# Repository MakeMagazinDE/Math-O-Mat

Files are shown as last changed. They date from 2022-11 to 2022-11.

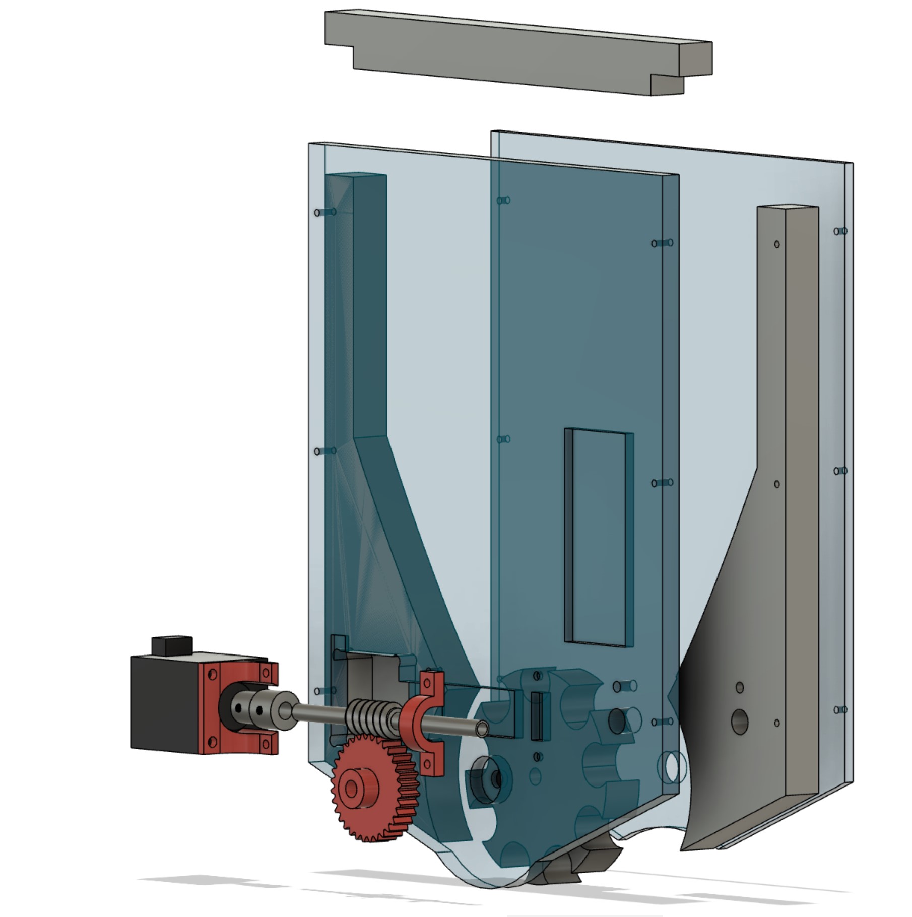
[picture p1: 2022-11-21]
Hardware/Explosionszeichnung.jpg

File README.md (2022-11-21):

GitHub Logo

Maker Media GmbH
*** 

# Math-O-Mat

stellt Übungsaufgaben fürs Kopfrechnen per Web-Quiz und belohnt richtige Antworten mit M&Ms.



Den vollständigen Artikel mit der Bauanleitung gibt es in der **[Make-Ausgabe 6/22 ab Seite 10](https://www.heise.de/select/make/2022/6/2216407360229342785) ** zu lesen

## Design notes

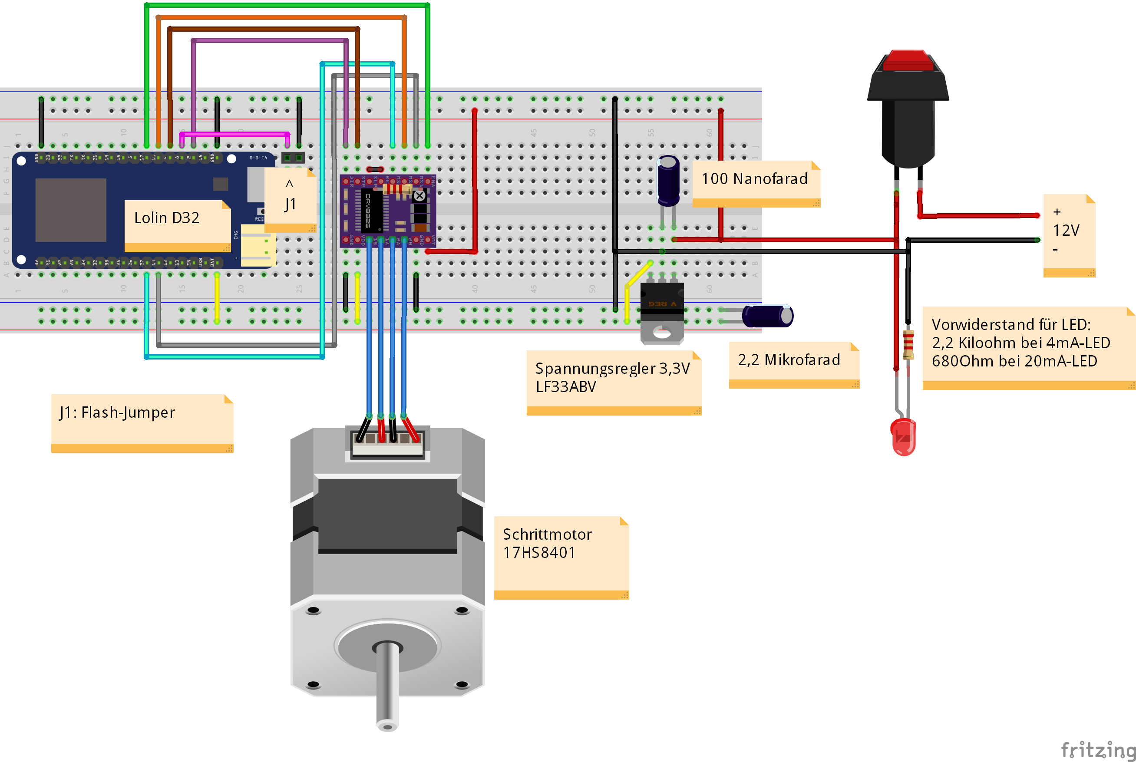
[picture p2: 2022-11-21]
Elektronik/MathOMat_Breadboard_Steckplatine.png

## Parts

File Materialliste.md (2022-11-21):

# Material

**Mechanik**

* Rückwand: Siebdruckplatte 270mm :x 360mm :x 10mm, Alternative für Laubsäge und Lasercutter: 2 Stück gleicher Maße aus  5mm MDF oder Sperrholz
* Trichter und Portionierer: Buche 230mm :x 415mm :x 20mm, Alternative für Laubsäge und Lasercutter: 4 Stück gleicher Maße aus  5mm MDF oder Sperrholz
* Acrylglas 255mm :x 325mm :x 5mm
* Gestell: Siebdruckplatte 290mm :x 250mm :x 10mm, Alternative für Laubsäge und Lasercutter: 2 Stück gleicher Maße aus  5mm MDF oder Sperrholz
* Aluminiumrohr 8mm als Achse für Schneckengetriebe
* Sechskantschraube M8x50, Gewindelänge 40mm, alternativ Gewindestange 50mm mit zwei gekonterten Muttern als Kopf, als Achse für den Portionierer 
* Stellschraube M4, ggf. auch eine Madenschraube
* 2 Kugellager Innendurchmesser 8mm, Aussendurchmesser 22 mm, Dicke 7mm
* 6 Schrauben M3x40mm mit Unterlegscheiben und Muttern
* Befestigungsmaterial für die Platine, etwa Schrauben, Distanzhülsen etc.
* 3D-Druckteile: Schnecke, Lagerhalter, Portioniererzahnrad, Motorhalter, Motorkupplung
* Holzschrauben mit Unterlegscheiben max 10mm lang (für die Deckplatte)
* Plastikstreifen 20mm breit, etwa 50 bis 80mm lang, als elastische Spaltabdeckung, etwa aus der Hülle eines Schnellhefters oder einer Plastikverpackung geschnitten –das Plastik muss einfach stabil genug sein, um überschüssige M&Ms abzustreifen. Kleben funktioniert gut, wobei die einfachste Lösung ist, den Streifen mit einer Heftzwecke auf das Holz zu heften.

Elektronik:

* ESP32 LOLIN D32 (andere ESP32-Typen sollten auch gehen) 
* A4988 Motortreiber
* Festspannungsregler LF33ABV
* 2 Elektrolytkondensatoren 0,1µF/2,2µF
* Einseitiges PCB und Header-Pins für Steckanschlüsse, flexible Brücken (Jumper)
* Netzteil 12V, mindestens 500mA, und ggf. Buchse dafür
* Ein/Ausschalter
* LED
* Widerstand 2,2 kOhm
* Schrittmotor Nema 17 (17HS8401 oder kleiner) Die meisten Nema 17 Motoren sollten funktionieren, meiner ist definitiv überdimensioniert aber ich hatte halt genau den zuhause. Ein kleinerer Schrittmotor, wie beispielsweise dieser (https://www.conrad.de/de/p/joy-it-schrittmotor-nema17-03-joy-it-0-2-nm-1-2-a-wellen-durchmesser-5-mm-2148831.html) reicht sicher aus. Damit die 3D-Druckteile passen, ist nur wichtig,  dass es eben ein Nema 17 mit den entsprechenden Anflanschgrössen ist.

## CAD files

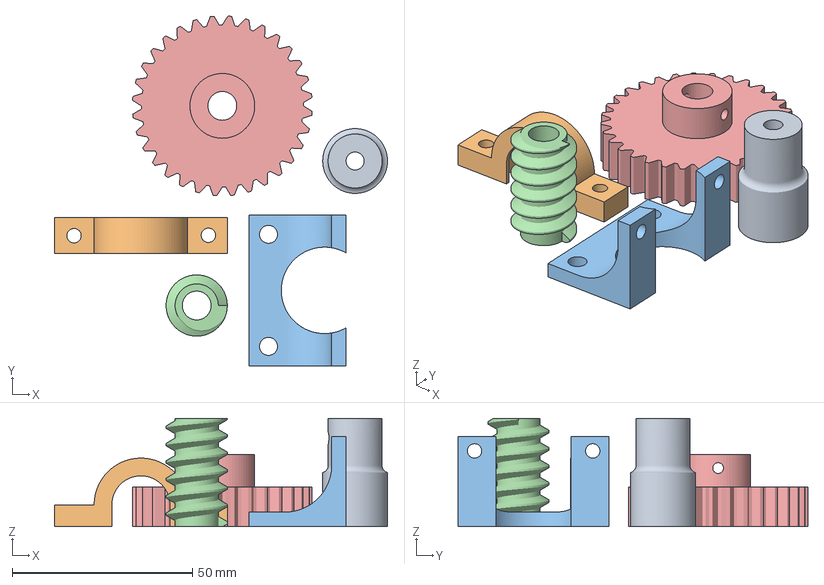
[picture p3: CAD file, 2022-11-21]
Hardware/3D_PrintFiles/3D_PrintParts_PrusaMK3_Project.3mf
92.5 x 97.2 x 30.0 mm
Kupplung.stl
LagerHalter.stl
Motorhalter.stl
Schnecke.stl
Zahnrad.stl

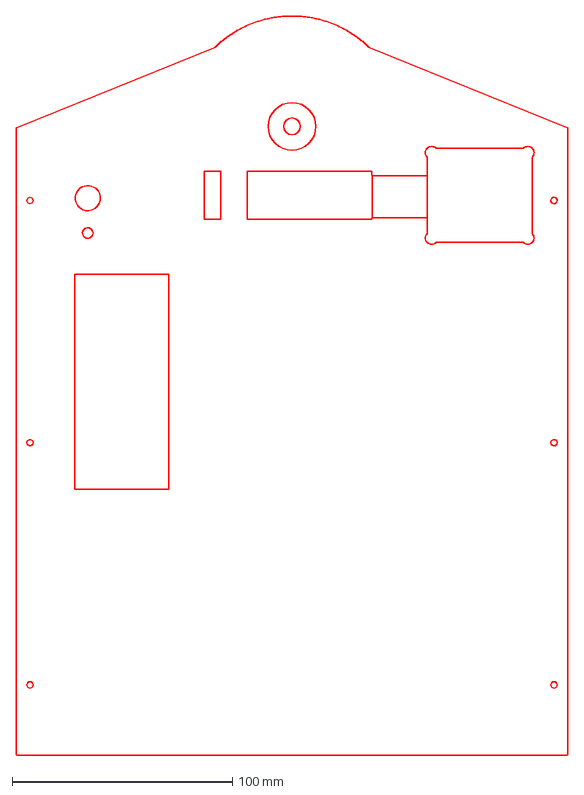
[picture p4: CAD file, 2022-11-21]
Hardware/DXF-Files/Laser_Rueckwand.dxf
250.3 x 335.6 mm

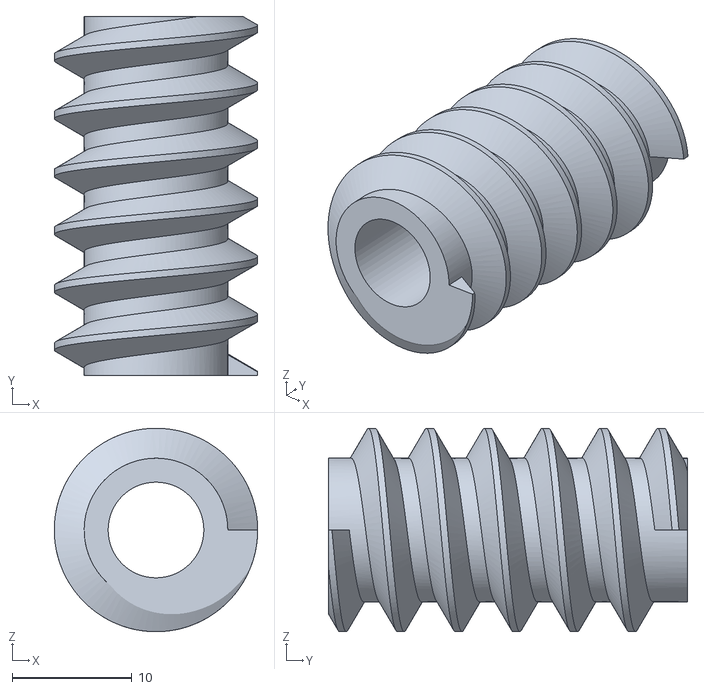
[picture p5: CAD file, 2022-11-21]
Hardware/3D_PrintFiles/Schnecke.stl
17.0 x 30.0 x 17.0

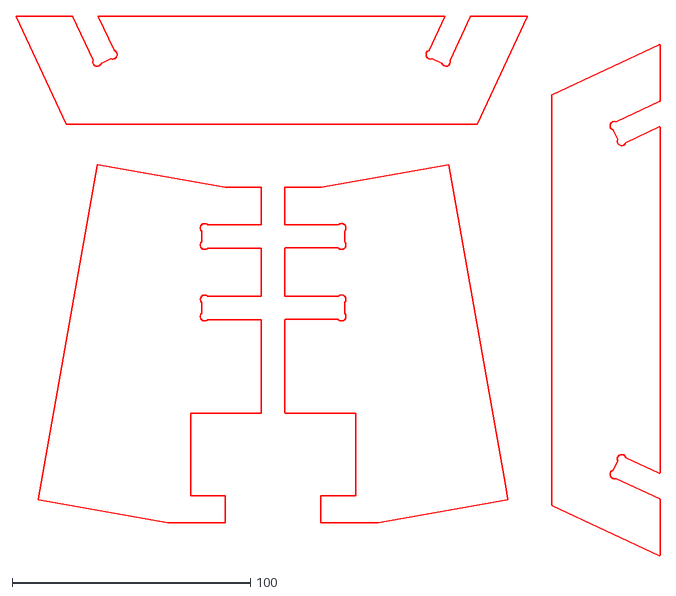
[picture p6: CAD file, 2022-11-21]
Hardware/DXF-Files/Laser_Staender.dxf
270.4 x 226.4

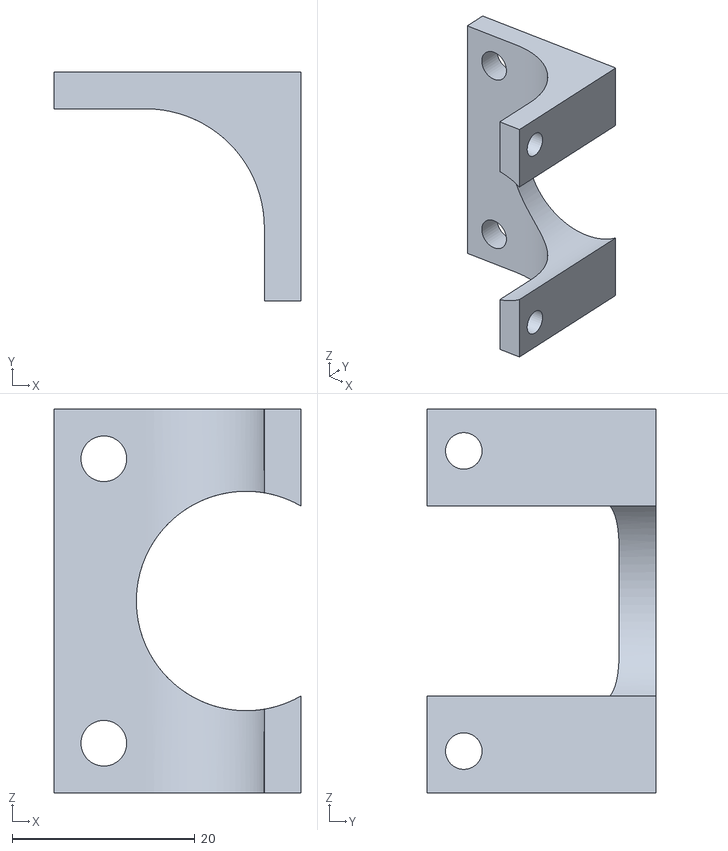
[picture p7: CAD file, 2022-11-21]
Hardware/3D_PrintFiles/Motorhalter.stl
27.0 x 25.0 x 42.0

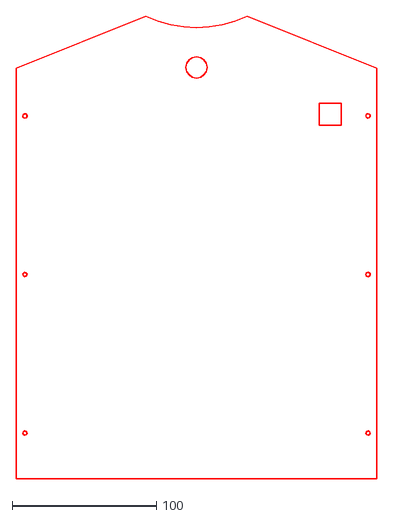
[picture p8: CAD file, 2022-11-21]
Hardware/DXF-Files/Laser_Acryl.dxf
250.3 x 321.1

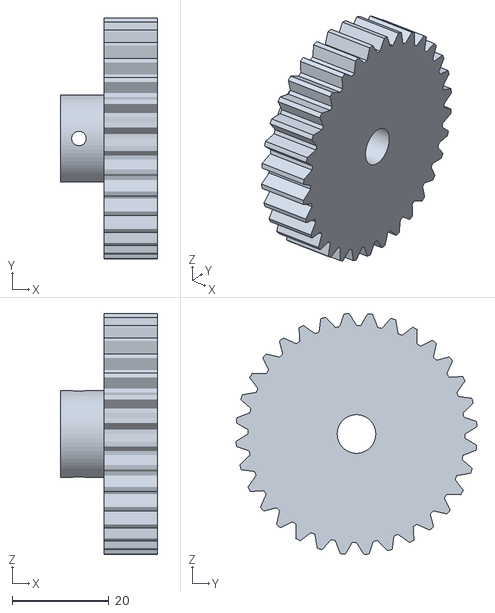
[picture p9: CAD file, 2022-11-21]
Hardware/3D_PrintFiles/Zahnrad.stl
20.0 x 49.9 x 49.9

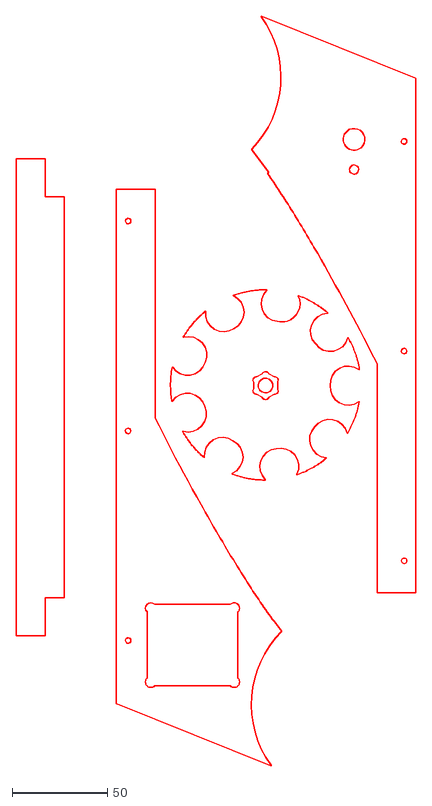
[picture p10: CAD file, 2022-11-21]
Hardware/DXF-Files/Laser_TrichterPortionierer.dxf
209.6 x 393.2

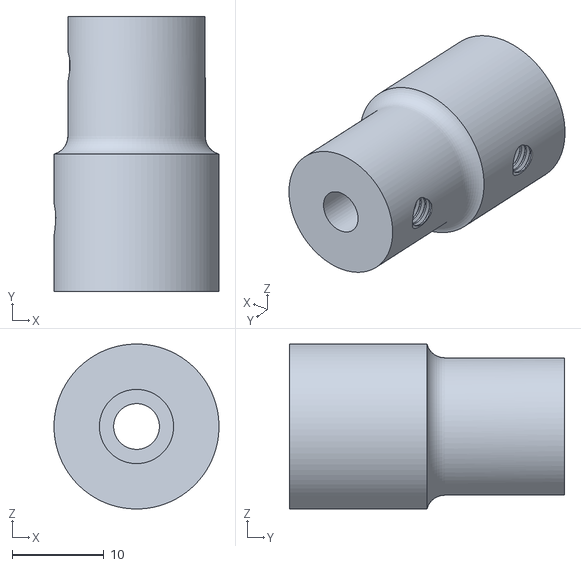
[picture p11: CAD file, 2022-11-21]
Hardware/3D_PrintFiles/Kupplung.stl
18.0 x 30.0 x 18.0

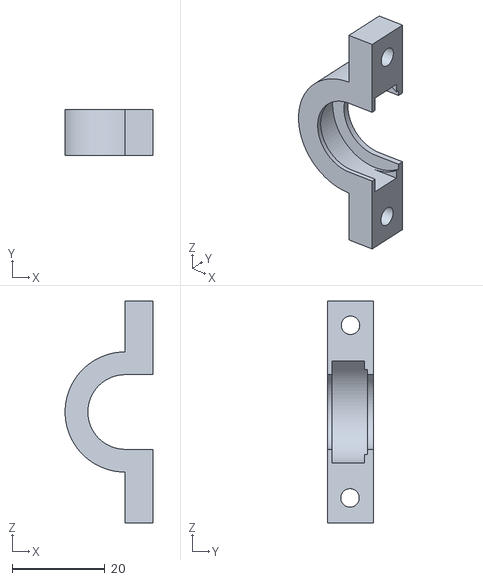
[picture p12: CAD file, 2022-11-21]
Hardware/3D_PrintFiles/LagerHalter.stl
19.0 x 10.0 x 48.0

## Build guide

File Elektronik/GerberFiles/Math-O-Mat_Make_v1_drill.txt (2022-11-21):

; NON-PLATED HOLES START AT T1
; THROUGH (PLATED) HOLES START AT T100
M48
INCH
T100C0.037694
T101C0.040000
T102C0.035000
T103C0.037722
T104C0.038000
T105C0.037750
T106C0.042000
%
T100
X002495Y005516
X003495Y005516
X007495Y005516
T101
X011400Y002366
X016715Y002366
X010022Y002366
X015337Y002366
X008644Y002366
X012778Y002366
T102
X017880Y008272
X027849Y002028
X028849Y002028
X011400Y007272
X009432Y007547
X023849Y002028
X029849Y002028
X029849Y011028
X035849Y011028
X028849Y011028
X031849Y011028
X011400Y008272
X034849Y002028
X025849Y002028
X033849Y002028
X009432Y003547
X030849Y002028
X020849Y011028
X030849Y011028
X025849Y011028
X022849Y011028
X033849Y011028
X027849Y011028
X032849Y002028
X023849Y011028
X032849Y011028
X026849Y011028
X034849Y011028
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

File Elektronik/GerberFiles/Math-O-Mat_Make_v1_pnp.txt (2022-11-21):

*Pick And Place List
*Company=
*Author=
*eMail=
*
*Project=Math-O-Mat_Make_v1
*Date=18:54:08
*CreatedBy=Fritzing 0.9.4.2019-12-01.CD-498-0-a1ffcea
*
*
*Coordinates in mm, always center of component
*Origin 0/0=Lower left corner of PCB
*Rotation in degree (0-360, math. pos.)
*
*No;Value;Package;X;Y;Rotation;Side;Name
1;2.2µF;100 mil [THT, electrolytic];28.9576;-19.7416;90;Bottom;C1
2;2.2k;THT;23.9576;-14.0916;-90;Bottom;R1
3;15.4;;9.76758;-5.01156;90;Bottom;17HS8401
4;;THT;40.5806;-6.51956;-90;Bottom;Vin
5;;THT;82.9576;-34.2816;180;Bottom;flash_jumper
6;;;12.4089;-20.321;90;Bottom;Stepper Driver
7;;THT;27.3346;-5.50356;90;Bottom;SW_LED_Term
8;;THT;47.9576;-6.28156;180;Bottom;spare1
9;;THT;47.9576;-13.2816;180;Bottom;spare2
10;2.2µF;100 mil [THT, electrolytic];46.6876;-21.0116;180;Bottom;C2
11;3.3V;TO220 [THT];38.4176;-16.5356;0;Bottom;LF33ABV
12;;DIP (Dual Inline) [THT];72.0076;-16.5816;-90;Bottom;LOLIN D32

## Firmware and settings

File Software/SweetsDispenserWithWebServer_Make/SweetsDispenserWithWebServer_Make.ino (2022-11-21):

// ---------------------------------------------------------------------------------------
//
// Code for Math-o-Mat (M&Ms dispenser). The code generates a Webpage with Websocket connection. 
// Random numbers are generated for a Math-quiz. Correct answers will enable the stepper-motor to dispense M&Ms from the storage.
// The code, written by Bernd Heisterkamp is based on the esp-websocket tutorial written by mo thunderz (https://www.youtube.com/watch?v=15X0WvGaVg8)
//
// For installation, the following libraries need to be installed:
// Websockets by Markus Sattler (can be tricky to find -> search for "Arduino Websockets"
// Stepper motor driver library A4988.h -> https://github.com/laurb9/StepperDriver/blob/master/src/A4988.h
// Arduino Json Library ArduinoJson.h -> Search libraries for ArduinoJson by Benoit Blanchon
// Library to connect to multiple Wifi-networks WifiMulti.h -> https://github.com/espressif/arduino-esp32/blob/master/libraries/WiFi/src/WiFiMulti.h

//
// ---------------------------------------------------------------------------------------

#include <WiFi.h>                 // needed to connect to WiFi
#include <WiFiMulti.h>            // allows definition of multiple wifi networks

#include <WebServer.h>            // needed to create a simple webserver
#include <WebSocketsServer.h>     // needed for instant communication between client and server through Websockets
#include <ArduinoJson.h>          // needed to convert and de-convert data into json format for easy web-socket communication
#include "A4988.h"                // needed to smoothly control the stepper motor with acceleration and decelleration

#define MOTOR_STEPS 400           // Defines the full-steps per resolution for the stepper-motor
#define MOTOR_ACCEL 2000          // Acceleration and deceleration values are always in FULL steps / s^2
#define MOTOR_DECEL 2000
#define MICROSTEPS 16             // Microstepping mode. 

// The following definitions define the IO-ports to control the stepper-driver
#define DIR 2                     // Stepper motor direction
#define STEP 4                    // Stepper motor stepping pulse
#define ENABLE 17                 // Pin to enable stepper-motor, low = active (!)
#define MS1 14                    // Microstepping mode switch 1
#define MS2 16                    // Microstepping mode switch 2
#define MS3 27                    // Microstepping mode switch 3

#define STEPS_EINELINSE -1281     // Steps to dispense a single M&M

A4988 stepper(MOTOR_STEPS, DIR, STEP, ENABLE, MS1, MS2, MS3);
int RPM = 150;              // Target RPM for cruise speed
bool bolNewGame = false;    // 
WiFiMulti wifiMulti;

// The String below "webpage" contains the complete HTML code that is sent to the client whenever someone connects to the webserver.
// It has been compressed using https://www.textfixer.com/html/compress-html-compression.php
// Make sure the HTML-code does not contain any double-quotes
String webpage = "<p>&nbsp;</p><p>&nbsp;</p><h1>Train your Brain !</h1><table><thead><tr><td><h4>No1</h4></td><td><h4>...</h4></td><td><h4>&nbsp;No2</h4></td><td><h4>=</h4></td><td><h4></h4></td><td><h4>Result</h4></td></tr></thead><tbody><tr><td style='text-align: center;'><p><strong><span id='sum1'>-</span></strong></p></td><td style='text-align: center;'><p><strong>+</strong></p></td><td style='text-align: center;'><p><strong><span id='sum2'>-</span></strong></p></td><td style='text-align: center;'><p><strong>=</strong></p></td><td><td><input type='number' name='lsgAdd' id='lsgAdd' max='9999' min='-9999' step='1'></td></td></tr><tr><td style='text-align: center;'><p><strong><span id='sub1'>-</span></strong></p></td><td style='text-align: center;'><p><strong>-</strong></p></td><td style='text-align: center;'><p><strong><span id='sub2'>-</span></strong></p></td><td style='text-align: center;'><p><strong>=</strong></p></td><td><td><input type='number' name='lsgSub' id='lsgSub' max='9999' min='-9999' step='1'></td></td></tr><tr><td style='text-align: center;'><p><strong><span id='prod1'>-</span></strong></p></td><td style='text-align: center;'><p><strong>*</strong></p></td><td style='text-align: center;'><p><strong><span id='prod2'>-</span></strong></p></td><td style='text-align: center;'><p><strong>=</strong></p></td><td><td><input type='number' name='lsgProd' id='lsgProd' max='9999' min='-9999' step='1'></td></td></tr><tr><td style='text-align: center;'><p><strong><span id='div1'>-</span></strong></p></td><td style='text-align: center;'><p><strong>/</strong></p></td><td style='text-align: center;'><p><strong><span id='div2'>-</span></strong></p></td><td style='text-align: center;'><p><strong>=</strong></p></td><td><td><input type='number' name='lsgDiv' id='lsgDiv' max='9999' min='-9999' step='1'></td></td></tr></tbody></table><p><button id='BTN_CHECK' type='button'>Check result </button></p><p><button id='BTN_SEND_BACK' type='button' hidden>Continue </button></p><script> var Socket; var obj; var CorrectAnswers; document.getElementById('BTN_CHECK').addEventListener('click', button_check_result); document.getElementById('BTN_SEND_BACK').addEventListener('click', button_send_back); function init() { Socket = new WebSocket('ws://' + window.location.hostname + ':81/'); Socket.onmessage = function(event) { processCommand(event); }; } function button_check_result() {CorrectAnswers = 0;document.getElementById('lsgAdd').setAttribute('disabled', '');document.getElementById('lsgSub').setAttribute('disabled', ''); document.getElementById('lsgProd').setAttribute('disabled', '');document.getElementById('lsgDiv').setAttribute('disabled', '');if (document.getElementById('lsgAdd').value == obj.LSGadd){CorrectAnswers += 1;document.getElementById('lsgAdd').style.color = 'green';} else {document.getElementById('lsgAdd').style.color = 'red';}if (document.getElementById('lsgSub').value == obj.LSGsub){CorrectAnswers += 1;document.getElementById('lsgSub').style.color = 'green';} else {document.getElementById('lsgSub').style.color = 'red';}if (document.getElementById('lsgProd').value == obj.LSGprod){CorrectAnswers += 1;document.getElementById('lsgProd').style.color = 'green';} else {document.getElementById('lsgProd').style.color = 'red';}if (document.getElementById('lsgDiv').value == obj.LSGdiv){CorrectAnswers += 1;document.getElementById('lsgDiv').style.color = 'green';} else {document.getElementById('lsgDiv').style.color = 'red';} console.log(CorrectAnswers);document.getElementById('BTN_CHECK').setAttribute('hidden', 'hidden');document.getElementById('BTN_SEND_BACK').removeAttribute('hidden'); } function button_send_back() { var loesungen = {count: CorrectAnswers,};ResetCounter = 0;document.getElementById('lsgAdd').value = '';document.getElementById('lsgSub').value = '';document.getElementById('lsgProd').value = '';document.getElementById('lsgDiv').value = '';document.getElementById('lsgAdd').style.color = 'black';document.getElementById('lsgSub').style.color = 'black';document.getElementById('lsgProd').style.color = 'black';document.getElementById('lsgDiv').style.color = 'black'; console.log(JSON.stringify(loesungen)); Socket.send(JSON.stringify(loesungen));document.getElementById('BTN_CHECK').removeAttribute('hidden');document.getElementById('BTN_SEND_BACK').setAttribute('hidden', 'hidden'); } function processCommand(event) {obj = JSON.parse(event.data); document.getElementById('sum1').innerHTML = obj.sum1; document.getElementById('sum2').innerHTML = obj.sum2; document.getElementById('sub1').innerHTML = obj.sub1; document.getElementById('sub2').innerHTML = obj.sub2; document.getElementById('prod1').innerHTML = obj.prod1; document.getElementById('prod2').innerHTML = obj.prod2; document.getElementById('div1').innerHTML = obj.div1; document.getElementById('div2').innerHTML = obj.div2;document.getElementById('lsgAdd').removeAttribute('disabled', '');document.getElementById('lsgSub').removeAttribute('disabled', ''); document.getElementById('lsgProd').removeAttribute('disabled', '');document.getElementById('lsgDiv').removeAttribute('disabled', ''); console.log(obj.sum1); console.log(obj.sum2); } window.onload = function(event) { init(); }</script></html>";

StaticJsonDocument<250> doc_tx;                       // Data send to WebPage
StaticJsonDocument<250> doc_rx;                       // Data received from WebPage

// Initialization of webserver and websocket
WebServer server(80);                                 // the server uses port 80 (standard port for webpages
WebSocketsServer webSocket = WebSocketsServer(81);    // the websocket uses port 81 (standard port for websockets

void setup() {
  Serial.begin(115200);                               // init serial port for debugging           
  unsigned long currentMillis = millis(); // call millis  and Get snapshot of time
  stepper.begin(RPM, MICROSTEPS);
  // Activate enable-pin on stepper-driver
  stepper.setEnableActiveState(LOW);
  /*
   * Set LINEAR_SPEED (accelerated) profile.
   */
  stepper.setSpeedProfile(stepper.LINEAR_SPEED, MOTOR_ACCEL, MOTOR_DECEL);
  stepper.disable();                                  // Disable stepper, it is only activated when dispensing M&Ms
  randomSeed(analogRead(0));                          // Assure truely random numbers
 
  // Add a line for each Wifi-network you'd like to connect to (e.g. Home, Fablab, Mobile-phone hotspot, etc.)
  wifiMulti.addAP("SSID-Network1", "Password1");  
  wifiMulti.addAP("SSID-Network2", "Password2");  
  wifiMulti.addAP("SSID-Network3", "Password3");  
  wifiMulti.addAP("SSID-Network4", "Password4");  
  Serial.println("Establishing connection to WiFi ");           // print SSID to the serial interface for debugging

  while (wifiMulti.run() != WL_CONNECTED) {             // wait until WiFi is connected
    delay(1000);
    Serial.print(".");
  }
  Serial.print("Connected to network with IP address: ");
  Serial.println(WiFi.localIP());                     // show IP address that the ESP32 has received from router
  
  server.on("/", []() {                               // define here what the webserver needs to do
    server.send(200, "text\html", webpage);           //    -> it needs to send out the HTML string "webpage" to the client
  });
  server.begin();                                     // start server
  webSocket.begin();                                  // start websocket
  webSocket.onEvent(webSocketEvent);                  // define a callback function 
                                                      // -> what does the ESP32 need to do when an event from the websocket is received? 
                                                      // -> run function "webSocketEvent()"
}

void loop() {
  server.handleClient();                              // Needed for the webserver to handle all clients
  if (bolNewGame == true) {
    newNumbers();
  }
  webSocket.loop();                                   // Update function for the webSockets 
}

void TurnWheel(int count){
  Serial.println("Correct Answers = " + String(count));
  stepper.enable();
  if (count == 4) {
    // With 4 correct answers dispens 2 M&Ms
    stepper.rotate(2 * STEPS_EINELINSE);
  } else if (count == 3) {
    // With 3 correct answers dispens 1 M&M
    stepper.rotate(1 * STEPS_EINELINSE);
  } 
  else {
    // Mocking the user with a short left-right rotation
    stepper.rotate(-0.5 * STEPS_EINELINSE);
    stepper.rotate(0.5 * STEPS_EINELINSE);
  }
  stepper.disable(); // Disable the stepper to save power.
}

void newNumbers(){
  bolNewGame = false;
  JsonObject object = doc_tx.to<JsonObject>(); //Define a JSON-object which is later filled with the new quiz-numbers
  String jsonString = "";

  // Generate random numbers for Math-quiz calculations and calculate correct solutions
  // Change random upper and lower range to make calculations more or less difficult
  long div1 = random(30,70);
  long div2 = div1;
  while (div1/div2 < 3){ 
    div2 = random(4,50);
  }
  div1 = div1 - (div1 % div2); 
  long sum1 = random(-100,100);   
  long sum2 = random(-100,100);
  long sub1 = random(-100,100);
  long sub2 = random(-100,100);
  long prod1 = random(3,20);
  long prod2 = random(3,50);
  long LSGadd = sum1 + sum2;
  long LSGsub = sub1 - sub2;
  long LSGprod = prod1 * prod2;
  long LSGdiv = div1 / div2;
  // Add generated numbers and solutions to JSON-object
  object ["sum1"] = sum1;
  object ["sum2"] = sum2;
  object ["LSGadd"] = LSGadd;
  object ["sub1"] = sub1;
  object ["sub2"] = sub2;
  object ["LSGsub"] = LSGsub;
  object ["prod1"] = prod1;
  object ["prod2"] = prod2;
  object ["LSGprod"] = LSGprod;
  object ["div1"] = div1;
  object ["div2"] = div2;
  object ["LSGdiv"] = LSGdiv;
  serializeJson(doc_tx, jsonString);
  Serial.println(jsonString);
  webSocket.broadcastTXT(jsonString); //Transfer numbers to web-page

}
void webSocketEvent(byte num, WStype_t type, uint8_t * payload, size_t length) {      // the parameters of this callback function are always the same -> num: id of the client who send the event, type: type of message, payload: actual data sent and length: length of payload
  switch (type) {                                     // switch on the type of information sent
    case WStype_DISCONNECTED:                         // if a client is disconnected, then type == WStype_DISCONNECTED
      Serial.println("Client " + String(num) + " disconnected");
      break;
    case WStype_CONNECTED:                            // if a client is connected, then type == WStype_CONNECTED
      Serial.println("Client " + String(num) + " connected");
      newNumbers(); // As soon as a client connects, new numbers are generated for the quiz.
      break;
    case WStype_TEXT:                                 // if a client has sent data, then type == WStype_TEXT
      DeserializationError error = deserializeJson(doc_rx, payload);
      if(error) {
        Serial.print("Deserialization failed");
        return;
      }
      else {
          const int g_count = doc_rx["count"];        // Count contains the number of correct answers (should be 4)
          TurnWheel(g_count);
          bolNewGame = true;
      }
      Serial.println("");
      break;
  }

}

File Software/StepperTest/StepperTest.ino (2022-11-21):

/*Example sketch to control a stepper motor with A4988 stepper motor driver and Arduino without a library. More info: https://www.makerguides.com */

// Define stepper motor connections and steps per revolution:
#define dirPin 2
#define stepPin 4
#define enablePin 17
#define MS1 14
#define MS2 16
#define MS3 27
#define stepsPerRevolution 200

void setup() {
  // Declare pins as output:
  pinMode(stepPin, OUTPUT);
  pinMode(dirPin, OUTPUT);
  pinMode(MS1, OUTPUT);
  pinMode(MS2, OUTPUT);
  pinMode(MS3, OUTPUT);
  pinMode(enablePin, OUTPUT);
  digitalWrite(enablePin, LOW);
  digitalWrite(MS1, HIGH);
  digitalWrite(MS2, HIGH);
  digitalWrite(MS3, HIGH);
 
}

void loop() {
  // Set the spinning direction clockwise:
  digitalWrite(dirPin, HIGH);

  // Spin the stepper motor 1 revolution slowly:
  for (int i = 0; i < stepsPerRevolution; i++) {
    // These four lines result in 1 step:
    digitalWrite(stepPin, HIGH);
    delayMicroseconds(2000);
    digitalWrite(stepPin, LOW);
    delayMicroseconds(2000);
  }
  digitalWrite(dirPin, LOW);
  for (int i = 0; i < stepsPerRevolution; i++) {
    // These four lines result in 1 step:
    digitalWrite(stepPin, HIGH);
    delayMicroseconds(2000);
    digitalWrite(stepPin, LOW);
    delayMicroseconds(2000);
  } 
}
